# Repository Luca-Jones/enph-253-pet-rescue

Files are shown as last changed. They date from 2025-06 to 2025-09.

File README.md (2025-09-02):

# enph-253-pet-rescue

## Overview
This project is a fully autonomous robot designed for ENPH 253 to compete in the 2025 Engineering Physics Robot Summer Competition at UBC. The cometition theme this year was Pet Rescue and goal was to drive around a course, find animal plushies in need of saving, retrieve them, and return them to the beginning of the course. Our team (team 4) of four Engineering Physics students designed and built the mechanical, electrical, and software components of this robot in 6 weeks to complete these tasks. Our team's strategy was to collect each of the pets into a basket and then lift that basket onto the zip-line to rescue them.

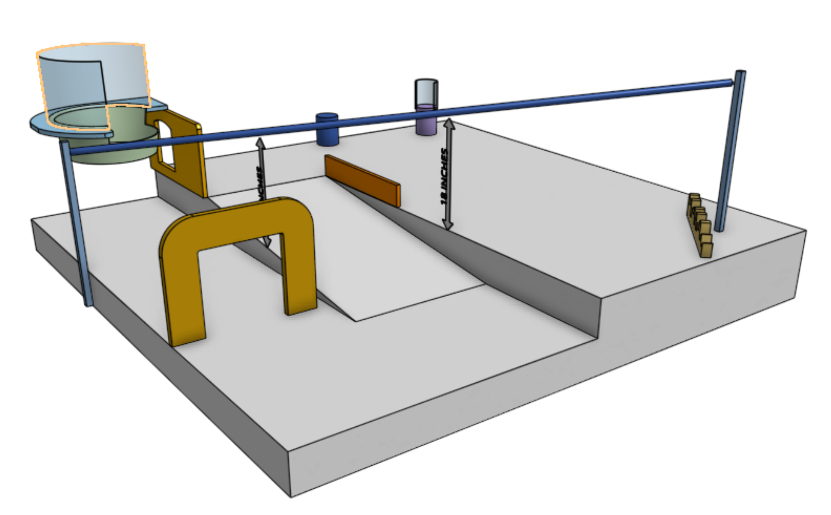
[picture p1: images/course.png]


## Meet the Team

- [Luca Jones](https://github.com/Luca-Jones)
- [Harchetan Chohan](https://github.com/HarchetanChohan)
- [Taichi Kamei](https://github.com/Ta1k25)
- [Coen Molyneaux](https://github.com/Coen-Molyneaux)

## Mechanical Design

The mechanical design was done with Onshape as our CAD tool. It is simple to use and allows for collaboration and version control. Many different manufacturing techniques were used such as 3D printing, laser jet cutting, water jet cutting, lathing, and milling.

### Chassis

The chassis was built out of hardboard and reinforced with water-jet cut aluminium bars. This component required the most communication to perfect as every other part of the robot needs to screw into it.

### Arm

The arm and claw together were responsible for grasping each pet and placing them into the bucket in the rear. The base of the arm is attached to a lazy suzan which is bolted to the chassis, allowing it to easily rotate and pick up pets in different directions. The base also had teeth to mesh with another gear driven by a DC motor. A magnetic rotation encoder was placed underneath the base which provided the feedback needed to create a servo and set an absolute position. The arm is designed as a 4 bar linkage, allowing the servo motors that drive its vertical movement to be located at its base rather than on the hinge. The claw also uses a 4 bar linkage so that the pinsors remain parallel and reach forwards as the claw closes.

### Cascading Lift

The cascading lift mechanism was responsible for lifting the basket that stored each of the pets onto the zip line that would bring them back to the start of the course. The cascading lift works by winding a rope around a spool and extending a cabinet slider through a series of pulleys. This system proved to be extremely effective. Unlike a scissor lift, the mechanical difficulty in lifting happens near the end of the motion rather than at the beginning, allowing us to easily provide enough torque to lift our desired weight.

## Electrical Design

### H-bridge Motor Driver

### IR Sensors

### I2C Buffer and Multiplexer

### Magnetic encoder

## Software Architecture

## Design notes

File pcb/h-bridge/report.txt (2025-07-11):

Error: Update symbol U15 from 'h-bridge-library:Terminal_Block_2POS' to 'h-bridge-library:Terminal_Block_2POS': *** symbol not found ***
Error: Update symbol U16 from 'h-bridge-library:Terminal_Block_2POS' to 'h-bridge-library:Terminal_Block_2POS': *** symbol not found ***
Update symbol R2 from 'Device:R' to 'Device:R': OK
Update symbol #PWR14 from 'power:GND' to 'power:GND': OK
Update symbol R8 from 'Device:R' to 'Device:R': OK
Update symbol #PWR11 from 'power:+3.3V' to 'power:+3.3V': OK
Update symbol U7 from 'h-bridge-library:2N3904' to 'h-bridge-library:2N3904': OK
Update symbol #PWR8 from 'power:GND' to 'power:GND': OK
Update symbol R10 from 'Device:R' to 'Device:R': OK
Update symbol #PWR7 from 'power:GND1' to 'power:GND1': OK
Update symbol R6 from 'Device:R' to 'Device:R': OK
Update symbol #PWR13 from 'power:+3.3V' to 'power:+3.3V': OK
Update symbol U6 from 'h-bridge-library:MCT6' to 'h-bridge-library:MCT6': OK
Update symbol #PWR15 from 'power:+12V' to 'power:+12V': OK
Update symbol U14 from 'h-bridge-library:IRFZ44' to 'h-bridge-library:IRFZ44': OK
Update symbol R13 from 'Device:R' to 'Device:R': OK
Update symbol U12 from 'h-bridge-library:IRFZ44' to 'h-bridge-library:IRFZ44': OK
Update symbol U11 from 'h-bridge-library:IRFZ44' to 'h-bridge-library:IRFZ44': OK
Update symbol U13 from 'h-bridge-library:IRFZ44' to 'h-bridge-library:IRFZ44': OK
Update symbol #PWR21 from 'power:+12V' to 'power:+12V': OK
Update symbol U9 from 'h-bridge-library:IRFZ44' to 'h-bridge-library:IRFZ44': OK
Update symbol C2 from 'Device:C' to 'Device:C': OK
Update symbol C1 from 'Device:C' to 'Device:C': OK
Update symbol U10 from 'h-bridge-library:IRFZ44' to 'h-bridge-library:IRFZ44': OK
Update symbol U8 from 'h-bridge-library:IRFZ44' to 'h-bridge-library:IRFZ44': OK
Update symbol U4 from 'h-bridge-library:IRFZ44' to 'h-bridge-library:IRFZ44': OK
Update symbol #PWR18 from 'power:+12V' to 'power:+12V': OK
Update symbol #PWR16 from 'power:GND' to 'power:GND': OK
Update symbol U17 from 'h-bridge-library:2N3904' to 'h-bridge-library:2N3904': OK
Update symbol R11 from 'Device:R' to 'Device:R': OK
Update symbol #PWR17 from 'power:GND' to 'power:GND': OK
Update symbol #PWR20 from 'power:GND' to 'power:GND': OK
Update symbol U18 from 'h-bridge-library:2N3904' to 'h-bridge-library:2N3904': OK
Update symbol #PWR19 from 'power:+12V' to 'power:+12V': OK
Update symbol R12 from 'Device:R' to 'Device:R': OK
Update symbol #PWR22 from 'power:GND' to 'power:GND': OK
Update symbol R14 from 'Device:R' to 'Device:R': OK
Update symbol U20 from 'h-bridge-library:2N3904' to 'h-bridge-library:2N3904': OK
Update symbol U19 from 'h-bridge-library:2N3904' to 'h-bridge-library:2N3904': OK
Update symbol #PWR23 from 'power:GND' to 'power:GND': OK
Update symbol R4 from 'Device:R' to 'Device:R': OK
Update symbol #PWR4 from 'power:GND' to 'power:GND': OK
Update symbol #PWR33 from 'power:+3.3V' to 'power:+3.3V': OK
Update symbol #PWR35 from 'power:GND1' to 'power:GND1': OK
Update symbol J26 from 'h-bridge-library:B3B-XH-A' to 'h-bridge-library:B3B-XH-A': OK
Update symbol #PWR34 from 'power:GND1' to 'power:GND1': OK
Update symbol J25 from 'h-bridge-library:B3B-XH-A' to 'h-bridge-library:B3B-XH-A': OK
Update symbol R22 from 'Device:R' to 'Device:R': OK
Update symbol R23 from 'Device:R' to 'Device:R': OK
Update symbol R21 from 'Device:R' to 'Device:R': OK
Update symbol R24 from 'Device:R' to 'Device:R': OK
Update symbol U5 from 'h-bridge-library:2N3904' to 'h-bridge-library:2N3904': OK
Update symbol #PWR10 from 'power:+12V' to 'power:+12V': OK
Update symbol #PWR9 from 'power:GND' to 'power:GND': OK
Update symbol #PWR3 from 'power:GND' to 'power:GND': OK
Update symbol R3 from 'Device:R' to 'Device:R': OK
Update symbol #PWR6 from 'power:+3.3V' to 'power:+3.3V': OK
Update symbol #PWR5 from 'power:GND' to 'power:GND': OK
Update symbol R5 from 'Device:R' to 'Device:R': OK
Update symbol #PWR24 from 'power:GND' to 'power:GND': OK
Update symbol R18 from 'Device:R' to 'Device:R': OK
Update symbol R17 from 'Device:R' to 'Device:R': OK
Update symbol U22 from 'h-bridge-library:2N3904' to 'h-bridge-library:2N3904': OK
Update symbol #PWR26 from 'power:GND' to 'power:GND': OK
Update symbol #PWR27 from 'power:+12V' to 'power:+12V': OK
Update symbol #PWR25 from 'power:GND' to 'power:GND': OK
Update symbol U21 from 'h-bridge-library:2N3904' to 'h-bridge-library:2N3904': OK
Update symbol R15 from 'Device:R' to 'Device:R': OK
Update symbol R16 from 'Device:R' to 'Device:R': OK
Update symbol #PWR29 from 'power:+12V' to 'power:+12V': OK
Update symbol R19 from 'Device:R' to 'Device:R': OK
Update symbol #PWR28 from 'power:GND' to 'power:GND': OK
Update symbol U23 from 'h-bridge-library:2N3904' to 'h-bridge-library:2N3904': OK
Update symbol U24 from 'h-bridge-library:2N3904' to 'h-bridge-library:2N3904': OK
Update symbol #PWR30 from 'power:GND' to 'power:GND': OK
Update symbol R20 from 'Device:R' to 'Device:R': OK
Update symbol #PWR31 from 'power:GND' to 'power:GND': OK
Update symbol #PWR32 from 'power:+12V' to 'power:+12V': OK
Update symbol #PWR1 from 'power:GND1' to 'power:GND1': OK
Update symbol U1 from 'h-bridge-library:MCT6' to 'h-bridge-library:MCT6': OK
Update symbol U3 from 'h-bridge-library:LT1161' to 'h-bridge-library:LT1161': OK
Update symbol U2 from 'h-bridge-library:MC33269T-3.3G' to 'h-bridge-library:MC33269T-3.3G': OK
Update symbol #PWR2 from 'power:+3.3V' to 'power:+3.3V': OK
Update symbol R1 from 'Device:R' to 'Device:R': OK
Update symbol R7 from 'Device:R' to 'Device:R': OK
Update symbol R9 from 'Device:R' to 'Device:R': OK
Update symbol #PWR12 from 'power:GND' to 'power:GND': OK

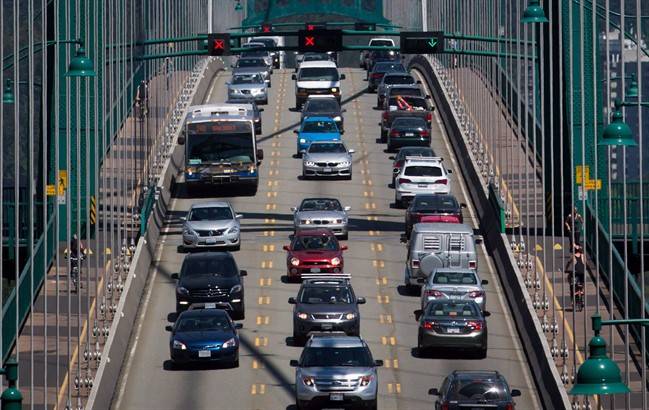
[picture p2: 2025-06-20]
cv-training/traffic.jpg

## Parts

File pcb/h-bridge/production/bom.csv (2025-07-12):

Designator | Footprint | Quantity | Value | LCSC Part #
C1, C2 | C_Disc_D4.3mm_W1.9mm_P5.00mm | 2 | 100nF
C3 | CP_Radial_D5.0mm_P2.50mm | 1 | 0.47uF
C4 | CP_Radial_D5.0mm_P2.50mm | 1 | 10uF
C5, C8, C9 | CP_Radial_D6.3mm_P2.50mm | 3 | 100uF
C6, C7 | C_Disc_D4.3mm_W1.9mm_P5.00mm | 2 | 100pF
J1 | JST_B2B-XH-A | 1 | B2B-XH-A
J2, J3 | JST_S2B-XH-A | 2 | S2B-XH-A
J5 | JST_B5B-XH-A | 1 | B5B-XH-A
R1, R2, R6, R7 | R_Axial_DIN0309_L9.0mm_D3.2mm_P12.70mm_Horizontal | 4 | 330R
R10, R11, R12, R19, R20, R3, R5, R8 | R_Axial_DIN0309_L9.0mm_D3.2mm_P12.70mm_Horizontal | 8 | 10K
R13, R14, R15, R16, R17, R18, R21, R22, R23, R24 | R_Axial_DIN0411_L9.9mm_D3.6mm_P12.70mm_Horizontal | 10 | 100k
R4, R9 | R_Axial_DIN0309_L9.0mm_D3.2mm_P12.70mm_Horizontal | 2 | 1k
U1, U6 | DIP-8_W7.62mm_Socket | 2 | MCT6
U10, U11, U12, U13, U14, U4, U8, U9 | TO-220-3_Vertical | 8 | IRFZ44
U17, U18, U19, U20, U21, U22, U23, U24, U5, U7 | TO-92 | 10 | 2N3904
U2 | TO-220-3_Vertical | 1 | MC33269T-3.3G
U3 | DIP-20_W7.62mm_Socket | 1 | LT1161

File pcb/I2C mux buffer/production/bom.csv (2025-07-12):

Designator | Footprint | Quantity | Value | LCSC Part #
C1, C2, C3 | C_Disc_D3.0mm_W1.6mm_P2.50mm | 3 | 100nF
C4 | C_Disc_D3.0mm_W1.6mm_P2.50mm | 1 | 10uF
J1 | JST_EH_B4B-EH-A_1x04_P2.50mm_Vertical | 1 | ToF Chassis
J2 | JST_EH_B4B-EH-A_1x04_P2.50mm_Vertical | 1 | ToF Claw
J3 | JST_PH_B5B-PH-K_1x05_P2.00mm_Vertical | 1 | Raspberry Pi
R1, R2, R3, R4, R5 | R_Axial_DIN0309_L9.0mm_D3.2mm_P12.70mm_Horizontal | 5 | 1k
R6 | R_Axial_DIN0309_L9.0mm_D3.2mm_P12.70mm_Horizontal | 1 | 10k
U1 | TSSOP-24_4.4x7.8mm_P0.65mm | 1 | TCA9548APWR
U2 | DGK0008A | 1 | TCA9617ADGKR

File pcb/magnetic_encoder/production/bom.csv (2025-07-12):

Designator | Footprint | Quantity | Value | LCSC Part #
C1 | C_Disc_D3.0mm_W1.6mm_P2.50mm | 1 | 100nF
C2 | CP_Radial_D5.0mm_P2.50mm | 1 | 10uF
J1 | JST_EH_S2B-EH_1x02_P2.50mm_Horizontal | 1 | Conn_01x02_Pin
J2 | JST_EH_S4B-EH_1x04_P2.50mm_Horizontal | 1 | Conn_01x04_Pin
R1, R2 | R_Axial_DIN0207_L6.3mm_D2.5mm_P7.62mm_Horizontal | 2 | 4.7K
U1 | SOIC-8_3.9x4.9mm_P1.27mm | 1 | ~

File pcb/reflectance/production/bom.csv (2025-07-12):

Designator | Footprint | Quantity | Value | LCSC Part #
J1, J2, J3 | JST_EH_B4B-EH-A_1x04_P2.50mm_Vertical | 3 | JCT 4pin
J4, J7 | JST_EH_B4B-EH-A_1x04_P2.50mm_Vertical | 2 | Reflectance Sensor 4
J6 | JST_EH_B3B-EH-A_1x03_P2.50mm_Vertical | 1 | Conn_01x03_Pin
J8 | JST_EH_B5B-EH-A_1x05_P2.50mm_Vertical | 1 | Conn_01x05_Pin
R1, R10, R15, R4, R7 | R_Axial_DIN0207_L6.3mm_D2.5mm_P7.62mm_Horizontal | 5 | 47k
R11, R14, R2, R5, R8 | R_Axial_DIN0207_L6.3mm_D2.5mm_P7.62mm_Horizontal | 5 | 330R
R12, R16, R3, R6, R9 | R_Axial_DIN0207_L6.3mm_D2.5mm_P7.62mm_Horizontal | 5 | 1k
RV1 | Potentiometer_Bourns_3296W_Vertical | 1 | 100k
U1, U2, U3, U4, U5 | DIP-8_W7.62mm_Socket_LongPads | 5 | LM311

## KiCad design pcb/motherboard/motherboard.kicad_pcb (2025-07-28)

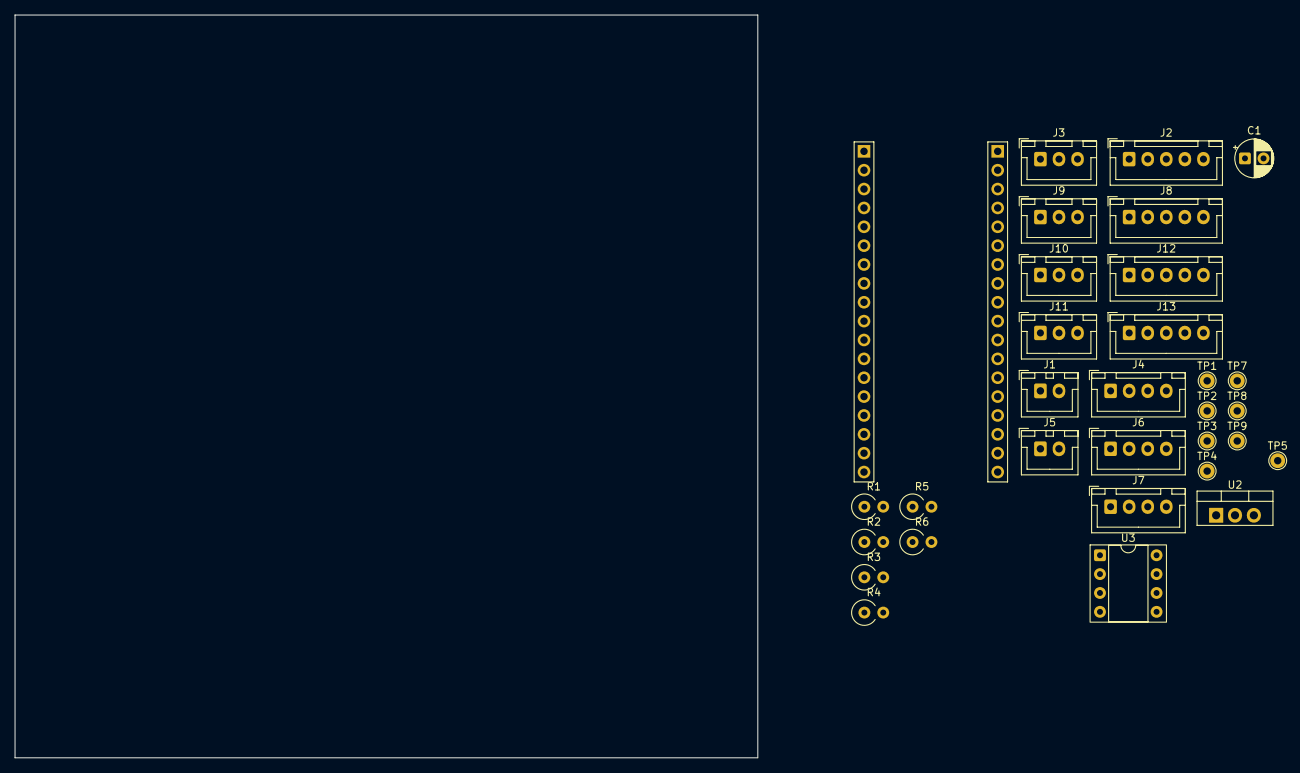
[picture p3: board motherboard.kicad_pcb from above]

Board: 2 copper layers, 100.0 x 100.0 mm, 31 parts (0 on the bottom side), 36 nets, no tracks yet.

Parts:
C1: 0.47uF; CP_Radial_D5.0mm_P2.50mm
J1, J5: B2B-XH-A; JST_XH_B2B-XH-A_1x02_P2.50mm_Vertical
J2, J8, J12, J13: B5B-XH-A; JST_XH_B5B-XH-A_1x05_P2.50mm_Vertical
J3, J9, J10, J11: B3B-XH-A; JST_XH_B3B-XH-A_1x03_P2.50mm_Vertical
J4, J6, J7: B4B-XH-A; JST_XH_B4B-XH-A_1x04_P2.50mm_Vertical
R1, R6: 1k; R_Axial_DIN0309_L9.0mm_D3.2mm_P2.54mm_Vertical
R2, R3, R4, R5: 100k; R_Axial_DIN0309_L9.0mm_D3.2mm_P2.54mm_Vertical
TP1: GPIO1; TestPoint_THTPad_D2.0mm_Drill1.0mm
TP2: GPIO3; TestPoint_THTPad_D2.0mm_Drill1.0mm
TP3: GPIO7; TestPoint_THTPad_D2.0mm_Drill1.0mm
TP4: GPIO8; TestPoint_THTPad_D2.0mm_Drill1.0mm
TP5: GPIO20; TestPoint_THTPad_D2.0mm_Drill1.0mm
TP7: GPIO 0; TestPoint_THTPad_D2.0mm_Drill1.0mm
TP8: GPIO 39; TestPoint_THTPad_D2.0mm_Drill1.0mm
TP9: GPIO 36; TestPoint_THTPad_D2.0mm_Drill1.0mm
U1: ESP32 PICO KIT; ESP32_PICO_KIT
U2: UA9805; TO-220-3_Vertical
U3: LM311; DIP-8_W7.62mm_Socket

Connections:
+3V3: J3.3, J4.1, J6.1, J7.1, J8.1, R1.1, R6.1, U1.1 (3V3), U1.21 (3V3)
+5V: J3.1, R3.2, U1.19 (5V), U2.3 (VOUT), U3.8 (V+)
+8V: J1.1, J9.1, J10.1, J11.1, U2.1 (VIN)
/BASE GEAR MOTOR DIR: J13.2, U1.31 (32)
/BASE GEAR MOTOR PWM: J13.1, U1.30 (33)
/BIG ARM SERVO: J9.2, U1.23 (4)
/CASCADE MOTOR DIR: J13.5, U1.33 (25)
/CASCADE MOTOR PWM: J13.4, U1.32 (26)
/CLAW SERVO: J11.2, U1.25 (15(BOOT_PULLUP))
/ECHO: J4.2, U1.11 (10)
/IR1: J2.1, U1.4 (37)
/IR2: J2.2, U1.5 (38)
/IR3: J2.3, U1.6 (34)
/IR4: J2.4, U1.7 (35)
/IR5: J2.5, U1.10 (9)
/LEFT MOTOR DIR: J12.2, U1.27 (12(BOOT_PULLDOWN))
/LEFT MOTOR PWM: J12.1, U1.26 (13)
/RIGHT MOTOR DIR: J12.5, U1.29 (27)
/RIGHT MOTOR PWM: J12.4, U1.28 (14)
/SCL: J6.2, J7.2, J8.2, U1.16 (22)
/SDA: J6.3, J7.3, J8.3, U1.17 (21)
/SMALL ARM SERVO: J10.2, U1.24 (2(BOOT_PULLDOWN))
/SWITCH1: R5.1, R6.2, U1.15 (19), U3.7
/TRIG: J4.3, U1.12 (5(BOOT_PULLUP))
GND: C1.2, J1.2, J3.2, J4.4, J5.2, J6.4, J7.4, J8.4, J8.5, J9.3, J10.3, J11.3, J12.3, J13.3, R4.1, U1.2 (GND), U1.20 (GND), U1.36 (GND), U2.2 (GND), U3.1 (GND), U3.4 (V-)
unnamed: J5.1, R1.2, R2.1
unnamed: TP7.1, U1.22 (0(BOOT_PULLUP))
unnamed: TP3.1, U1.13 (7)
unnamed: TP4.1, U1.14 (8)
unnamed: TP5.1, U1.18 (20)
unnamed: TP2.1, U1.9 (RX0(GPIO3))
unnamed: TP1.1, U1.8 (TX0(GPIO1))
unnamed: TP8.1, U1.34 (VN(GPIO39))
unnamed: TP9.1, U1.35 (VP(GPIO36))
unnamed: R3.1, R4.2, R5.2, U3.2 (+)
unnamed: C1.1, R2.2, U3.3 (-)

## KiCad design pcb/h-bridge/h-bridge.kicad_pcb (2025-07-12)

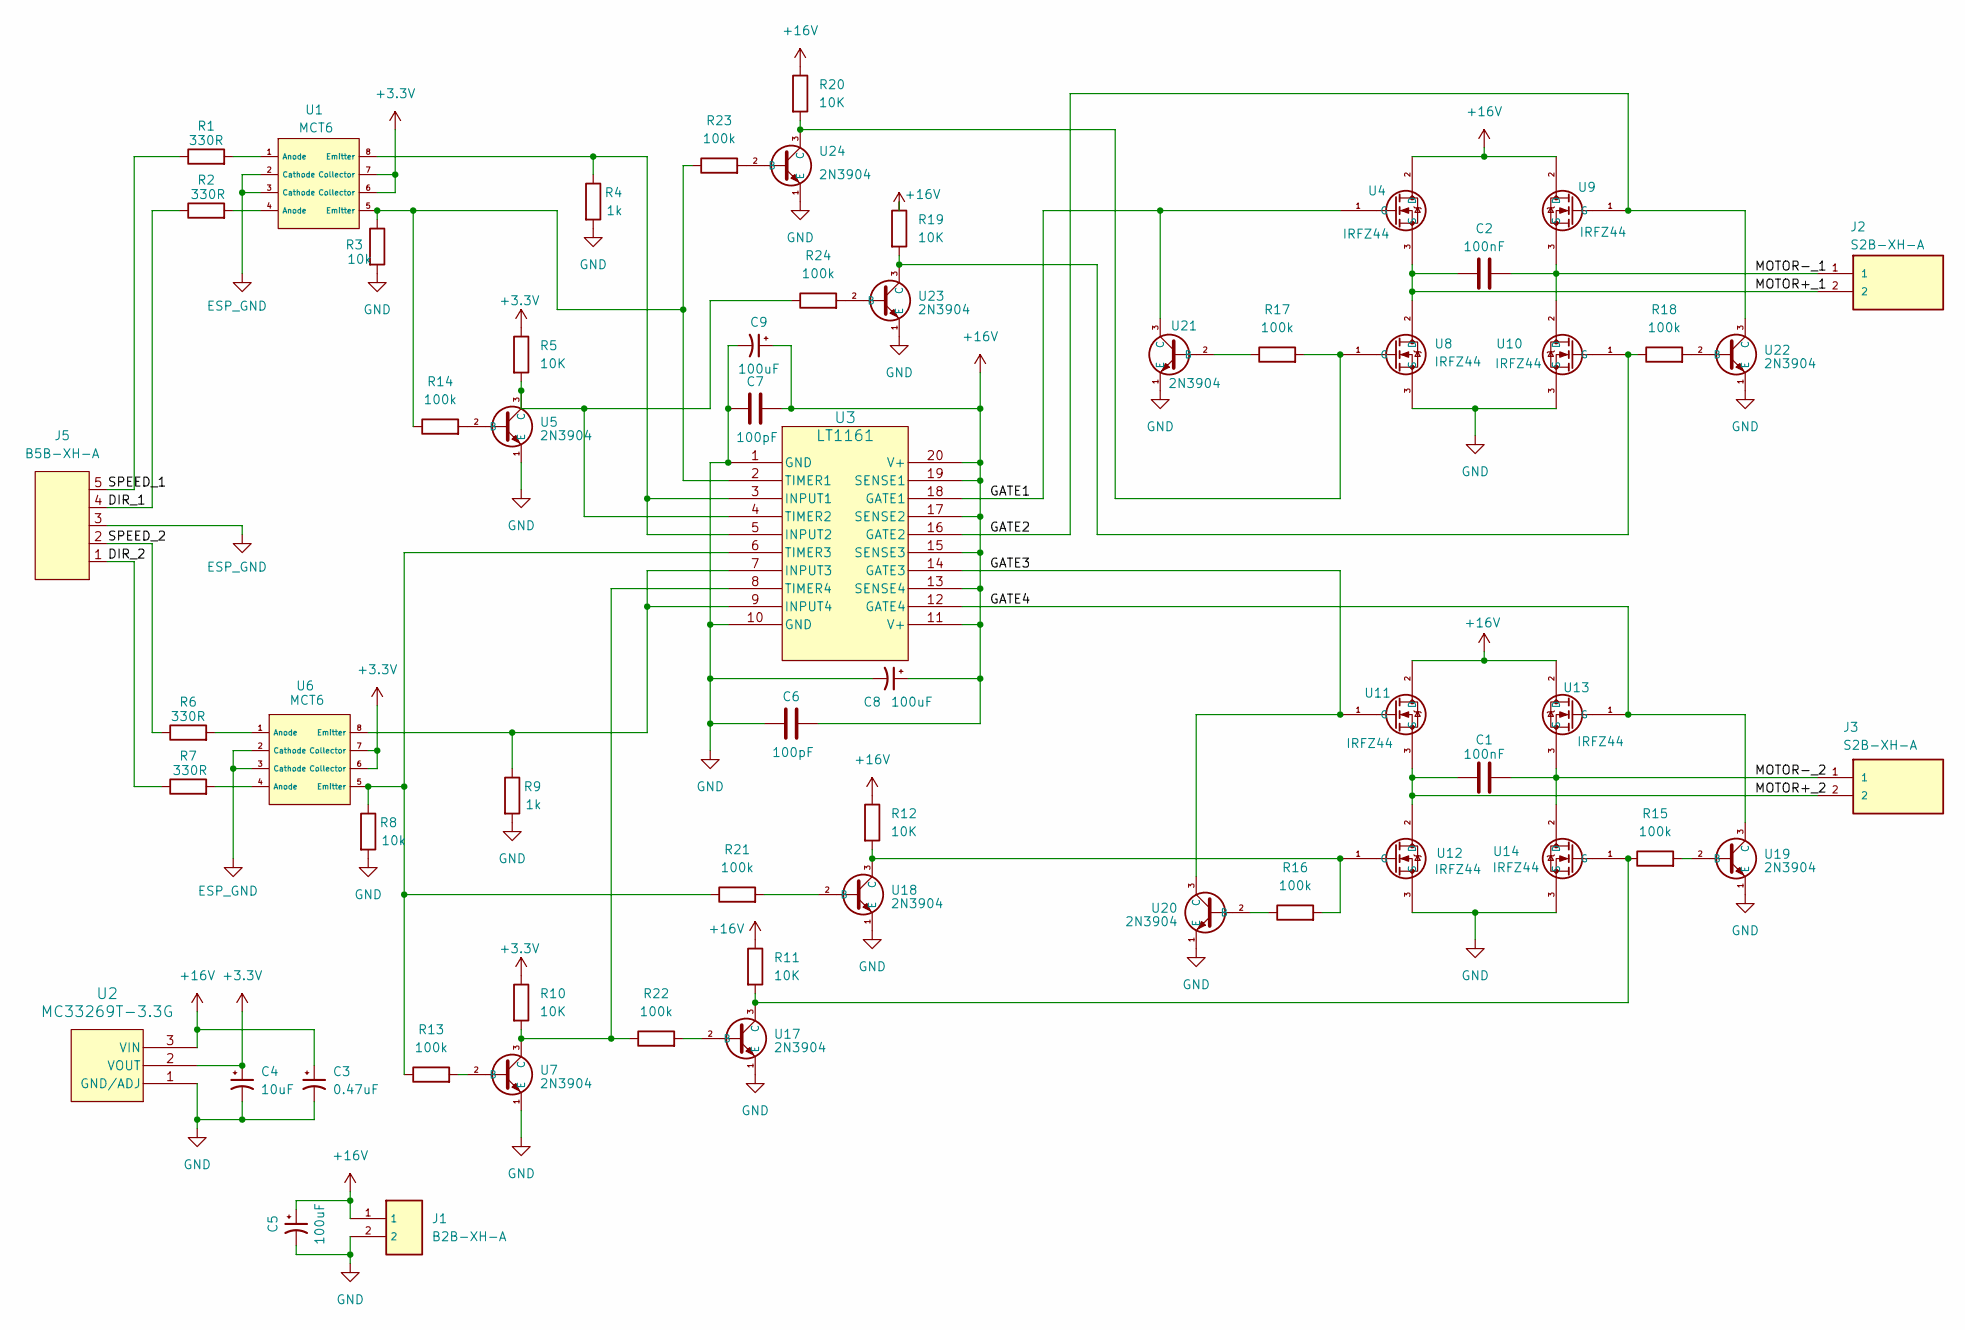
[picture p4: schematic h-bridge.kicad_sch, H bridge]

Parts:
C1, C2: 100nF; C_Disc_D3.0mm_W1.6mm_P2.50mm
C3: 0.47uF; CP_Radial_D5.0mm_P2.50mm
C4: 10uF; CP_Radial_D5.0mm_P2.50mm
C5, C8, C9: 100uF; CP_Radial_D6.3mm_P2.50mm
C6, C7: 100pF; C_Disc_D3.0mm_W1.6mm_P2.50mm
J1: B2B-XH-A; JST_B2B-XH-A
J2, J3: S2B-XH-A; JST_S2B-XH-A
J5: B5B-XH-A; JST_B5B-XH-A
R1, R2, R6, R7: 330R; R_Axial_DIN0309_L9.0mm_D3.2mm_P12.70mm_Horizontal
R3, R8: 10k; R_Axial_DIN0309_L9.0mm_D3.2mm_P12.70mm_Horizontal
R4, R9: 1k; R_Axial_DIN0309_L9.0mm_D3.2mm_P12.70mm_Horizontal
R5, R10, R11, R12, R19, R20: 10K; R_Axial_DIN0309_L9.0mm_D3.2mm_P12.70mm_Horizontal
R13, R14, R15, R16, R17, R18, R21, R22, R23, R24: 100k; R_Axial_DIN0411_L9.9mm_D3.6mm_P12.70mm_Horizontal
U1, U6: MCT6; DIP-8_W7.62mm_Socket
U2: MC33269T-3.3G; TO-220-3_Vertical
U3: LT1161; DIP-20_W7.62mm_Socket
U4, U8, U9, U10, U11, U12, U13, U14: IRFZ44; TO-220-3_Vertical
U5, U7, U17, U18, U19, U20, U21, U22, U23, U24: 2N3904; TO-92

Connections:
+3.3V: C4.1, R5.1, R10.1, U1.6 (Collector), U1.7 (Collector), U2.2 (VOUT), U6.6 (Collector), U6.7 (Collector)
+16V: C3.1, C5.1, C6.2, C7.2, C8.1, C9.1, J1.1, R11.1, R12.1, R19.1, R20.1, U2.3 (VIN), U3.11 (V+), U3.13 (SENSE4), U3.15 (SENSE3), U3.17 (SENSE2), U3.19 (SENSE1), U3.20 (V+), U4.2 (D), U9.2 (D), U11.2 (D), U13.2 (D)
/DIR_1: J5.4, R2.1
/DIR_2: J5.1, R7.1
/GATE1: U3.18 (GATE1), U4.1 (G), U21.3 (C)
/GATE2: U3.16 (GATE2), U9.1 (G), U22.3 (C)
/GATE3: U3.14 (GATE3), U11.1 (G), U20.3 (C)
/GATE4: U3.12 (GATE4), U13.1 (G), U19.3 (C)
/MOTOR+_1: C2.1, J2.2, U4.3 (S), U8.2 (D)
/MOTOR+_2: C1.1, J3.2, U11.3 (S), U12.2 (D)
/MOTOR-_1: C2.2, J2.1, U9.3 (S), U10.2 (D)
/MOTOR-_2: C1.2, J3.1, U13.3 (S), U14.2 (D)
/SPEED_1: J5.5, R1.1
/SPEED_2: J5.2, R6.1
ESP_GND: J5.3, U1.2 (Cathode), U1.3 (Cathode), U6.2 (Cathode), U6.3 (Cathode)
GND: C3.2, C4.2, C5.2, C6.1, C7.1, C8.2, C9.2, J1.2, R3.2, R4.2, R8.2, R9.2, U2.1 (GND/ADJ), U3.1 (GND), U3.10 (GND), U5.1 (E), U7.1 (E), U8.3 (S), U10.3 (S), U12.3 (S), U14.3 (S), U17.1 (E), U18.1 (E), U19.1 (E), U20.1 (E), U21.1 (E), U22.1 (E), U23.1 (E), U24.1 (E)
unnamed: R1.2, U1.1 (Anode)
unnamed: R2.2, U1.4 (Anode)
unnamed: R6.2, U6.1 (Anode)
unnamed: R7.2, U6.4 (Anode)
unnamed: R4.1, U1.8 (Emitter), U3.3 (INPUT1), U3.5 (INPUT2)
unnamed: R9.1, U3.7 (INPUT3), U3.9 (INPUT4), U6.8 (Emitter)
unnamed: R3.1, R14.1, R23.1, U1.5 (Emitter), U3.2 (TIMER1)
unnamed: R5.2, R24.1, U3.4 (TIMER2), U5.3 (C)
unnamed: R8.1, R13.1, R21.1, U3.6 (TIMER3), U6.5 (Emitter)
unnamed: R10.2, R22.1, U3.8 (TIMER4), U7.3 (C)
unnamed: R14.2, U5.2 (B)
unnamed: R13.2, U7.2 (B)
unnamed: R18.1, R19.2, U10.1 (G), U23.3 (C)
unnamed: R12.2, R16.2, U12.1 (G), U18.3 (C)
unnamed: R11.2, R15.1, U14.1 (G), U17.3 (C)
unnamed: R22.2, U17.2 (B)
unnamed: R21.2, U18.2 (B)
unnamed: R15.2, U19.2 (B)
unnamed: R16.1, U20.2 (B)
unnamed: R17.1, U21.2 (B)
unnamed: R18.2, U22.2 (B)
unnamed: R24.2, U23.2 (B)
unnamed: R23.2, U24.2 (B)
unnamed: R17.2, R20.2, U8.1 (G), U24.3 (C)

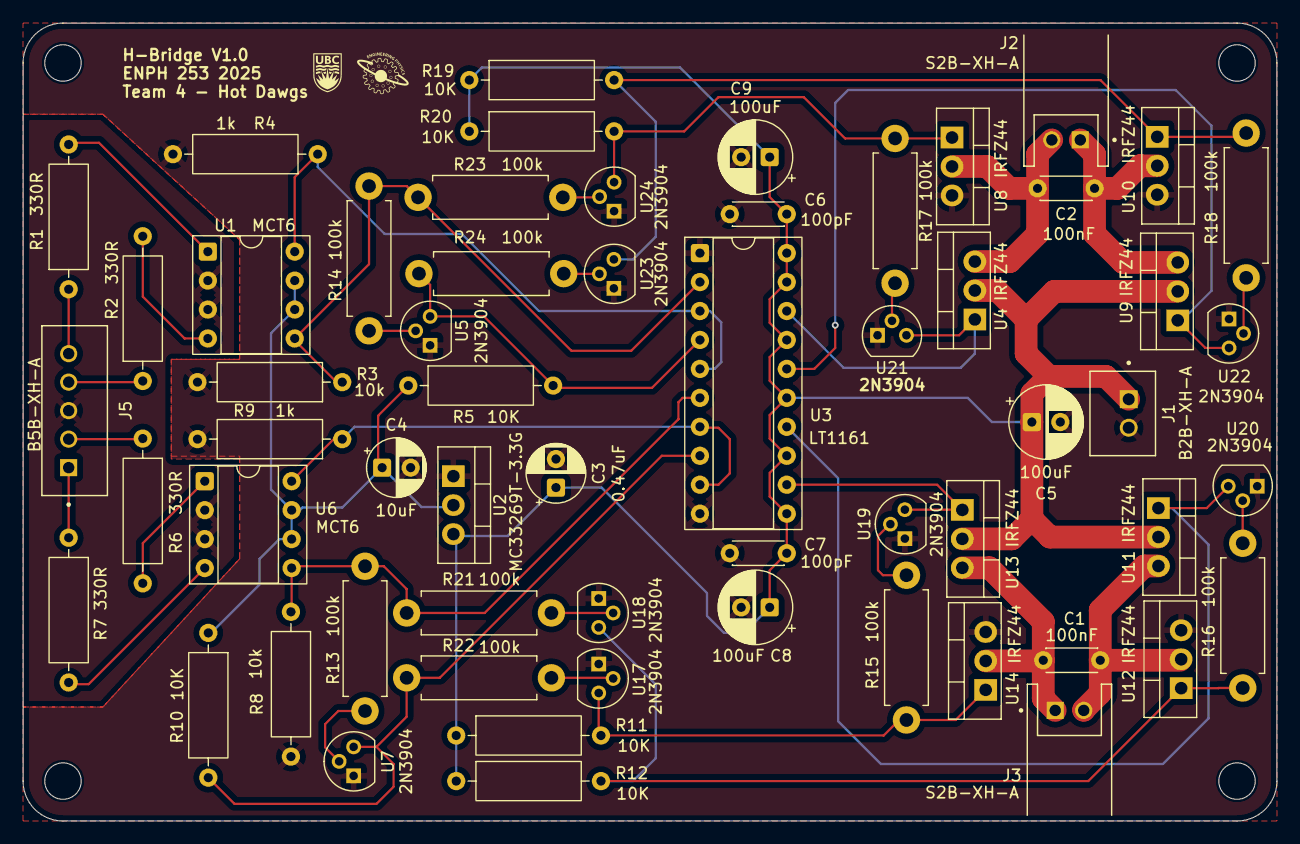
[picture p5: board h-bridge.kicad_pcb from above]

Board: 2 copper layers, 110.0 x 70.0 mm, 59 parts (0 on the bottom side), 40 nets.

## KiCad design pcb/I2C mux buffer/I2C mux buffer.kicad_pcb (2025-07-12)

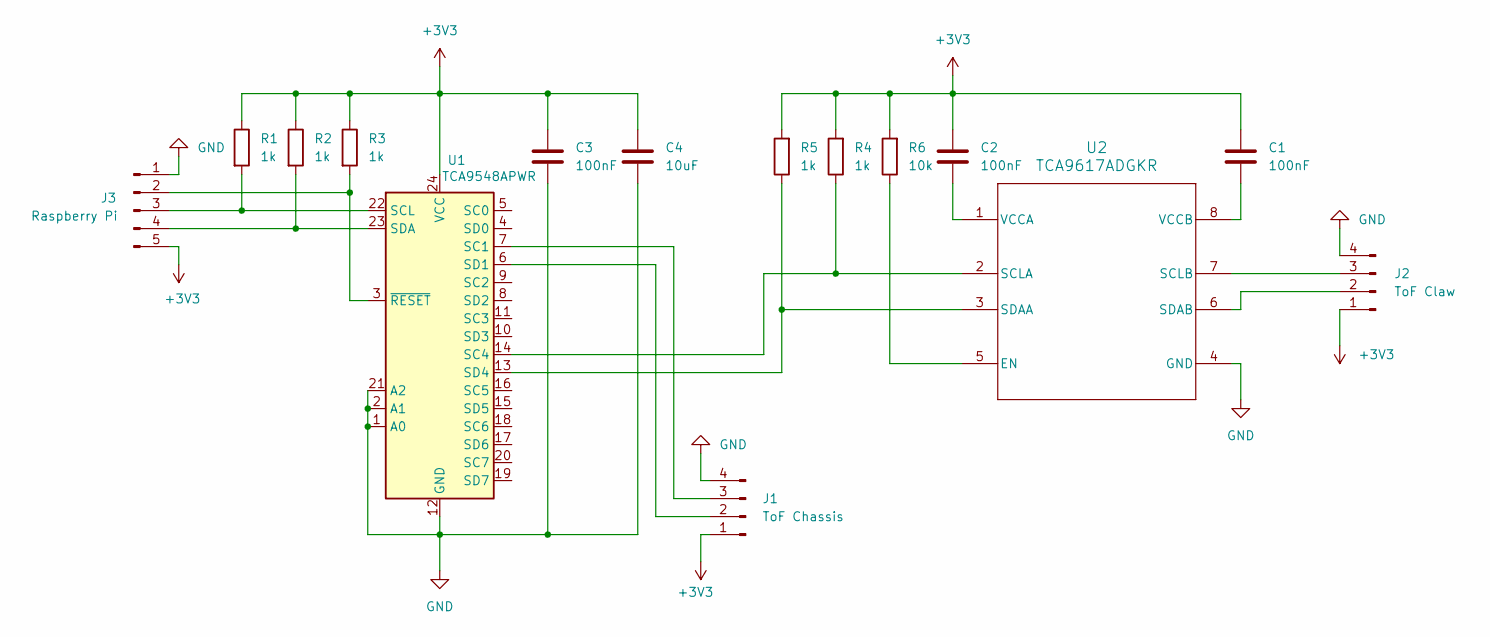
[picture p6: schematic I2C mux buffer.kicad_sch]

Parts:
C1, C2, C3: 100nF; C_Disc_D3.0mm_W1.6mm_P2.50mm
C4: 10uF; C_Disc_D3.0mm_W1.6mm_P2.50mm
J1: ToF Chassis; JST_EH_B4B-EH-A_1x04_P2.50mm_Vertical
J2: ToF Claw; JST_EH_B4B-EH-A_1x04_P2.50mm_Vertical
J3: Raspberry Pi; JST_PH_B5B-PH-K_1x05_P2.00mm_Vertical
R1, R2, R3, R4, R5: 1k; R_Axial_DIN0309_L9.0mm_D3.2mm_P12.70mm_Horizontal
R6: 10k; R_Axial_DIN0309_L9.0mm_D3.2mm_P12.70mm_Horizontal
U1: TCA9548APWR; TSSOP-24_4.4x7.8mm_P0.65mm
U2: TCA9617ADGKR; DGK0008A

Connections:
+3V3: C1.1, C2.1, C3.1, C4.1, J1.1, J2.1, J3.5, R1.1, R2.1, R3.1, R4.2, R5.2, R6.2, U1.24 (VCC)
GND: C3.2, C4.2, J1.4, J2.4, J3.1, U1.1 (A0), U1.2 (A1), U1.12 (GND), U1.21 (A2), U2.4 (GND)
unnamed: J1.2, U1.6 (SD1)
unnamed: J1.3, U1.7 (SC1)
unnamed: J2.2, U2.6 (SDAB)
unnamed: J2.3, U2.7 (SCLB)
unnamed: J3.2, R3.2, U1.3 (~RESET)
unnamed: J3.3, R1.2, U1.22 (SCL)
unnamed: J3.4, R2.2, U1.23 (SDA)
unnamed: R4.1, U1.14 (SC4), U2.2 (SCLA)
unnamed: R5.1, U1.13 (SD4), U2.3 (SDAA)
unnamed: R6.1, U2.5 (EN)
unnamed: C2.2, U2.1 (VCCA)
unnamed: C1.2, U2.8 (VCCB)

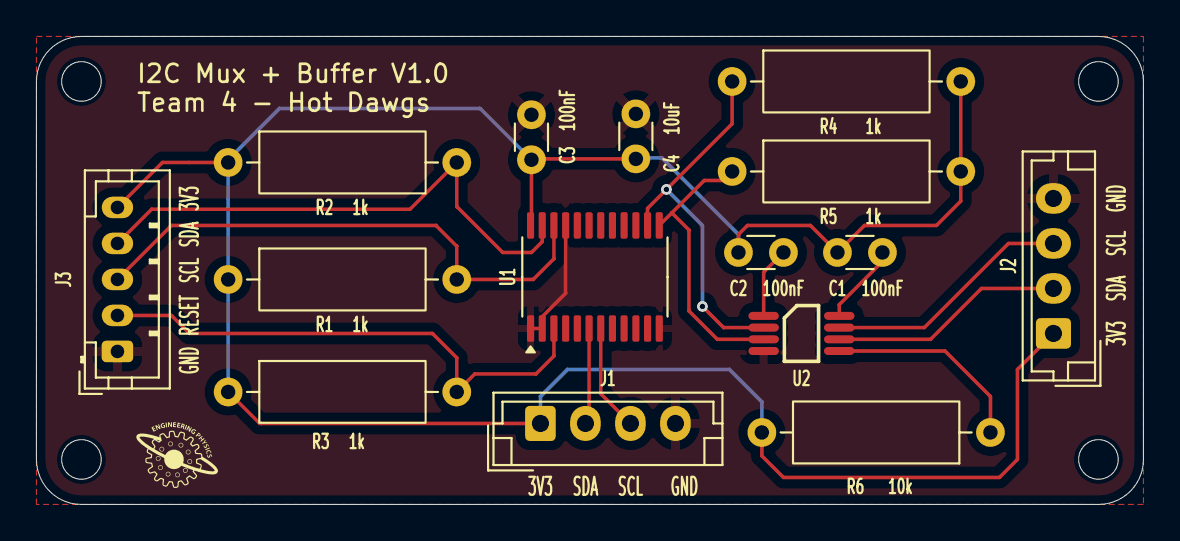
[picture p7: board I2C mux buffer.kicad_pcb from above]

Board: 2 copper layers, 61.5 x 26.0 mm, 15 parts (0 on the bottom side), 14 nets.

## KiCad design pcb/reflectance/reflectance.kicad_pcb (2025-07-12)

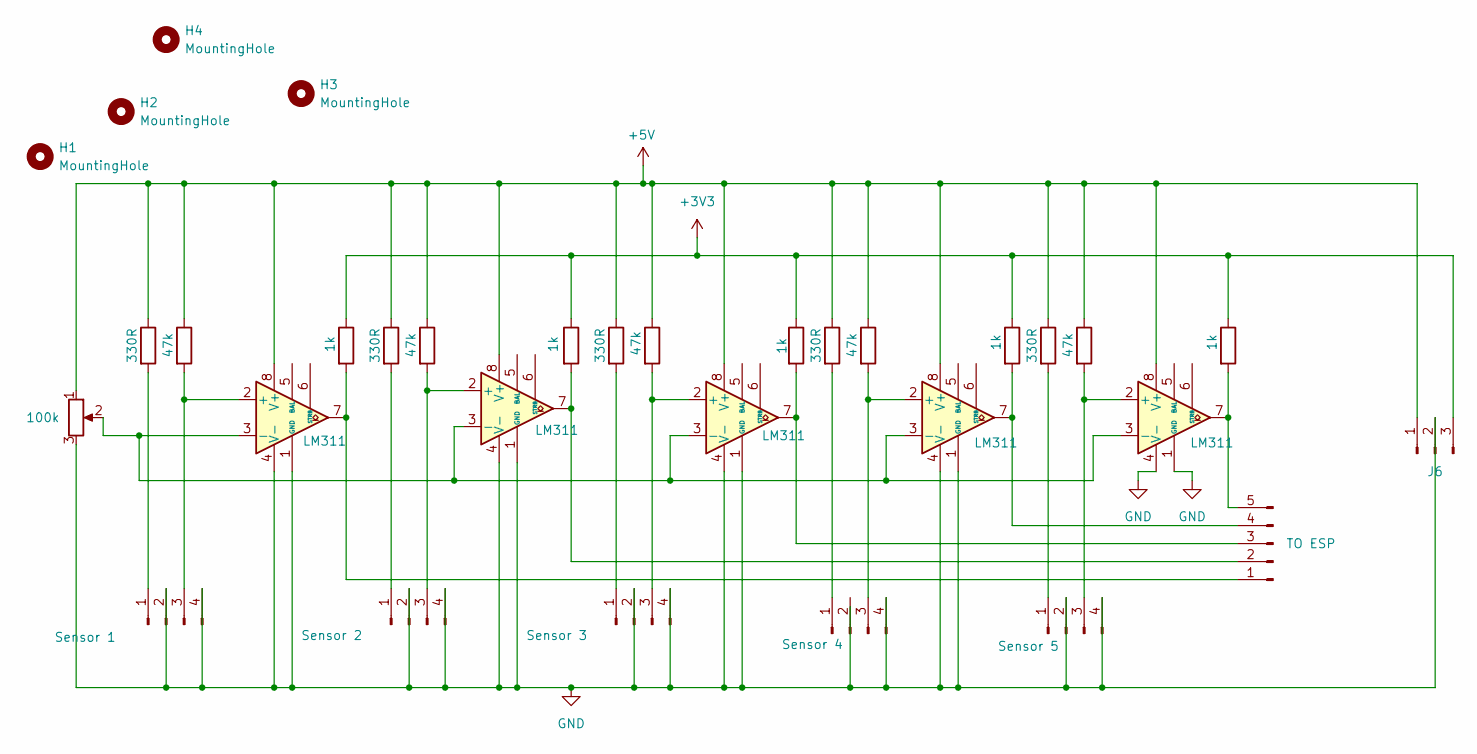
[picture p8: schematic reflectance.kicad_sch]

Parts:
H1, H2, H3, H4: MountingHole; MountingHole_3.2mm_M3
J1, J3: JCT 4pin; JST_EH_B4B-EH-A_1x04_P2.50mm_Vertical
J2: JCt 4pin; JST_EH_B4B-EH-A_1x04_P2.50mm_Vertical
J4, J7: Reflectance Sensor 4; JST_EH_B4B-EH-A_1x04_P2.50mm_Vertical
J6: Conn_01x03_Pin; JST_EH_B3B-EH-A_1x03_P2.50mm_Vertical
J8: Conn_01x05_Pin; JST_EH_B5B-EH-A_1x05_P2.50mm_Vertical
R1, R4, R7, R10, R15: 47k; R_Axial_DIN0207_L6.3mm_D2.5mm_P7.62mm_Horizontal
R2, R5, R8, R11, R14: 330R; R_Axial_DIN0207_L6.3mm_D2.5mm_P7.62mm_Horizontal
R3, R6, R9, R12, R16: 1k; R_Axial_DIN0207_L6.3mm_D2.5mm_P7.62mm_Horizontal
RV1: 100k; Potentiometer_Bourns_3296W_Vertical
U1, U2, U3, U4, U5: LM311; DIP-8_W7.62mm_Socket_LongPads

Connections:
+3V3: J6.3, R3.1, R6.1, R9.1, R12.1, R16.1
+5V: J6.1, R1.1, R2.1, R4.1, R5.1, R7.1, R8.1, R10.1, R11.1, R14.1, R15.1, RV1.1, U1.8 (V+), U2.8 (V+), U3.8 (V+), U4.8 (V+), U5.8 (V+)
GND: J1.2, J1.4, J2.2, J2.4, J3.2, J3.4, J4.4, J6.2, J7.2, J7.4, RV1.3, U1.1 (GND), U1.4 (V-), U2.1 (GND), U2.4 (V-), U3.1 (GND), U3.4 (V-), U4.1 (GND), U4.4 (V-), U5.1 (GND), U5.4 (V-)
unnamed: J1.1, R2.2
unnamed: J1.3, R1.2, U2.2 (+)
unnamed: J2.1, R5.2
unnamed: J2.3, R4.2, U1.2 (+)
unnamed: J3.1, R8.2
unnamed: J3.3, R7.2, U3.2 (+)
unnamed: J4.1, R11.2
unnamed: J4.3, R10.2, U4.2 (+)
unnamed: J7.1, R14.2
unnamed: J7.3, R15.2, U5.2 (+)
unnamed: J8.1, R3.2, U2.7
unnamed: J8.2, R6.2, U1.7
unnamed: J8.3, R9.2, U3.7
unnamed: J8.4, R12.2, U4.7
unnamed: J8.5, R16.2, U5.7
unnamed: RV1.2, U1.3 (-), U2.3 (-), U3.3 (-), U4.3 (-), U5.3 (-)

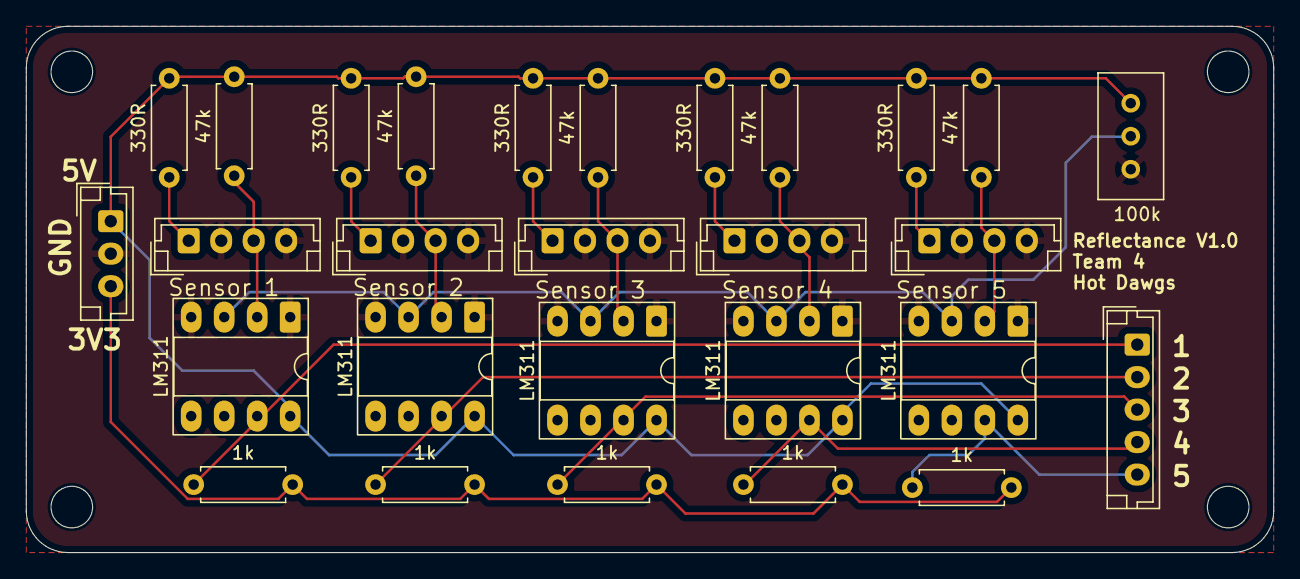
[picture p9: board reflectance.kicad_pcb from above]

Board: 2 copper layers, 96.0 x 40.5 mm, 32 parts (0 on the bottom side), 19 nets.

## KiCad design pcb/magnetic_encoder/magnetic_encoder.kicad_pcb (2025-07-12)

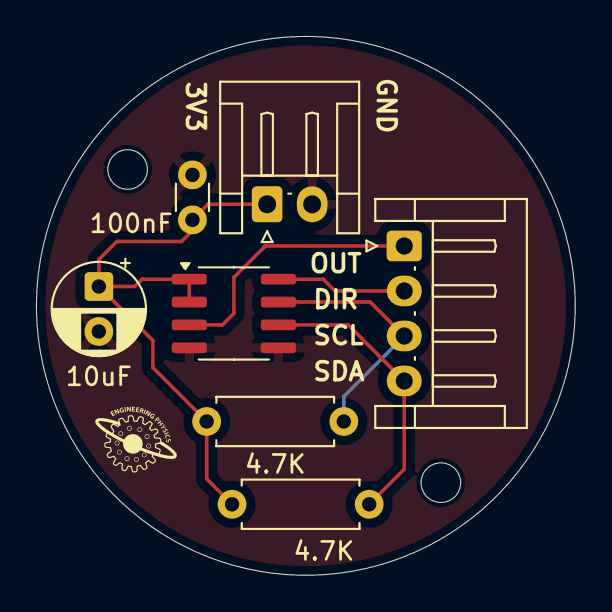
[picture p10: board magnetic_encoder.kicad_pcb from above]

Board: 2 copper layers, 29.9 x 29.9 mm, 9 parts (0 on the bottom side), 6 nets.

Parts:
C1: 100nF; C_Disc_D3.0mm_W1.6mm_P2.50mm
C2: 10uF; CP_Radial_D5.0mm_P2.50mm
H1, H3: MountingHole; MountingHole_2.2mm_M2
J1: Conn_01x02_Pin; JST_EH_S2B-EH_1x02_P2.50mm_Horizontal
J2: Conn_01x04_Pin; JST_EH_S4B-EH_1x04_P2.50mm_Horizontal
R1, R2: 4.7K; R_Axial_DIN0207_L6.3mm_D2.5mm_P7.62mm_Horizontal
U1: SOIC-8_3.9x4.9mm_P1.27mm

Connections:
+3.3V: C1.1, C2.1, J1.1, R1.1, R2.1, U1.1 (VDD5V), U1.2 (VDD3V3)
GND: C1.2, C2.2, J1.2, U1.4 (GND), U1.5 (PGO)
unnamed: J2.1, U1.3 (OUT)
unnamed: J2.2, U1.8 (DIR)
unnamed: J2.3, R2.2, U1.7 (SCL)
unnamed: J2.4, R1.2, U1.6 (SDA)

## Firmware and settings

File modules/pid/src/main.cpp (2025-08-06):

#include <WebServer.h>
#include <WiFi.h>
#include <Arduino.h>


// WiFi credentials
const char *ssid = "hot_dawgs_esp";
const char *password = "team4_da_best_on_top";


#define FORWARD LOW
#define BACKWARD HIGH


// Web server
WebServer server(80);


// PID parameters (tunable via web or serial)
float Kp = 25.0, Ki = 0.0, Kd = 0.0;
float recoveryRatio = 0.6; // Ratio of base speed for recovery spin
float targetPosition = 0.0;
float currentPosition = 0.0;
float previousError = 0.0;
float integral = 0.0;
float lastPosition = 0.0;
float deadband = 0.1;
float integralDecay = 0.95;
float maxIntegral = 100.0;
bool targetChanged = false;


unsigned long lastPIDTime = 0;
bool lastPID[5];
unsigned long sampleTime = 30;


const int SENSOR_LEFT_LEFT = 37;
const int SENSOR_LEFT      = 38;
const int SENSOR_CENTER    = 34;
const int SENSOR_RIGHT     = 35;
const int SENSOR_RIGHT_RIGHT = 9;


const int MOTOR_LEFT_PWM  = 14;
const int MOTOR_LEFT_DIR  = 27;
const int MOTOR_RIGHT_PWM = 13;
const int MOTOR_RIGHT_DIR = 12;


const int PWM_FREQ = 1000;
const int PWM_RESOLUTION = 8;
const int PWM_CHANNEL_LEFT = 0;
const int PWM_CHANNEL_RIGHT = 1;


int baseSpeed = 100;
int maxSpeed = 255;
int minSpeed = 0;


// Tasks
TaskHandle_t wifiTaskHandle;
TaskHandle_t controlTaskHandle;


// HTML page
const char htmlPage[] PROGMEM = R"rawliteral(
<!DOCTYPE html>
<html>
<head>
   <title>ESP32 PID Tuning</title>
   <style>
     body { font-family: sans-serif; margin: 20px; }
     .controls { margin-bottom: 20px; }
     .control-group { margin: 10px 0; }
     label { margin-right: 10px; }
     input[type="number"] { width: 80px; padding: 5px; }
     button { padding: 8px 16px; background: #007bff; color: white; border: none; cursor: pointer; }
     button:hover { background: #0056b3; }
     .sensor-values {
       margin: 20px 0;
       padding: 10px;
       background: #f8f9fa;
       border-radius: 5px;
     }
     .sensor {
       display: inline-block;
       margin: 0 10px;
       text-align: center;
     }
     .sensor-indicator {
       width: 20px;
       height: 20px;
       border-radius: 50%;
       margin: 5px auto;
       background-color: #ddd;
     }
     .sensor-active {
       background-color: #28a745;
     }
     .status {
       margin: 20px 0;
       padding: 10px;
       background: #e9ecef;
       border-radius: 5px;
     }
   </style>
</head>
<body>
   <h2>ESP32 PID Tuning</h2>


   <div class="sensor-values">
     <h3>Sensor Values</h3>
     <div class="sensor">
       <div id="sensor-ll" class="sensor-indicator"></div>
       <div>LL</div>
     </div>
     <div class="sensor">
       <div id="sensor-l" class="sensor-indicator"></div>
       <div>L</div>
     </div>
     <div class="sensor">
       <div id="sensor-c" class="sensor-indicator"></div>
       <div>C</div>
     </div>
     <div class="sensor">
       <div id="sensor-r" class="sensor-indicator"></div>
       <div>R</div>
     </div>
     <div class="sensor">
       <div id="sensor-rr" class="sensor-indicator"></div>
       <div>RR</div>
     </div>
   </div>


   <div class="status">
     <h3>Status</h3>
     <p>Current Position: <span id="current-pos">0.0</span></p>
     <p>Error: <span id="error">0.0</span></p>
     <p>PID Output: <span id="pid-output">0.0</span></p>
   </div>


   <div class="controls">
     <div class="control-group">
       <label>Kp: <input id="kp" type="number" value="100.0" step="0.1"></label>
       <label>Ki: <input id="ki" type="number" value="0.5" step="0.1"></label>
       <label>Kd: <input id="kd" type="number" value="20.0" step="0.1"></label>
       <button onclick="setPID()">Set PID</button>
     </div>
    
     <div class="control-group">
       <label>Recovery Ratio: <input id="recovery-ratio" type="number" value="0.6" step="0.1" min="0.1" max="1.0"></label>
       <button onclick="setRecoveryRatio()">Set Recovery Ratio</button>
     </div>
    
     <div class="control-group">
       <label>Base Speed: <input id="base-speed" type="number" value="100" min="0" max="255"></label>
       <button onclick="setSpeed()">Set Speed</button>
     </div>
   </div>
    <script>
     function setPID() {
       const kp = document.getElementById('kp').value;
       const ki = document.getElementById('ki').value;
       const kd = document.getElementById('kd').value;
       fetch(`/setPID?kp=${kp}&ki=${ki}&kd=${kd}`)
         .then(response => {
           if (!response.ok) {
             console.error('Failed to set PID parameters');
           }
         })
         .catch(error => console.error('Error:', error));
     }
      function setRecoveryRatio() {
       const ratio = document.getElementById('recovery-ratio').value;
       fetch(`/setRecoveryRatio?value=${ratio}`)
         .then(response => {
           if (!response.ok) {
             console.error('Failed to set recovery ratio');
           }
         })
         .catch(error => console.error('Error:', error));
     }
    
     function setSpeed() {
       const speed = document.getElementById('base-speed').value;
       fetch(`/setSpeed?value=${speed}`)
         .then(response => {
           if (!response.ok) {
             console.error('Failed to set speed');
           }
         })
         .catch(error => console.error('Error:', error));
     }
      function updateSensors(sensors) {
       document.getElementById('sensor-ll').className = 'sensor-indicator' + (sensors.ll ? ' sensor-active' : '');
       document.getElementById('sensor-l').className = 'sensor-indicator' + (sensors.l ? ' sensor-active' : '');
       document.getElementById('sensor-c').className = 'sensor-indicator' + (sensors.c ? ' sensor-active' : '');
       document.getElementById('sensor-r').className = 'sensor-indicator' + (sensors.r ? ' sensor-active' : '');
       document.getElementById('sensor-rr').className = 'sensor-indicator' + (sensors.rr ? ' sensor-active' : '');
     }
    
     function updateStatus(data) {
       document.getElementById('current-pos').textContent = data.current.toFixed(2);
       document.getElementById('error').textContent = data.error.toFixed(2);
       document.getElementById('pid-output').textContent = data.output.toFixed(2);
     }


     function update() {
       fetch('/status')
         .then(res => res.json())
         .then(data => {
           updateSensors(data.sensors);
           updateStatus(data);
         })
         .catch(error => {
           console.error('Error fetching status:', error);
         });
     }
      window.addEventListener('load', function() {
       setInterval(update, 200);
     });
   </script>
</body>
</html>
)rawliteral";


// ==== Helper Functions ====


void controlMotors(float pidOutput) {
 int leftSpeed = baseSpeed - pidOutput;
 int rightSpeed = baseSpeed + pidOutput;


 leftSpeed = constrain(leftSpeed, -maxSpeed, maxSpeed);
 rightSpeed = constrain(rightSpeed, -maxSpeed, maxSpeed);


 // Stop motors first
 ledcWrite(PWM_CHANNEL_LEFT, 0);
 ledcWrite(PWM_CHANNEL_RIGHT, 0);
 delayMicroseconds(100);


 // Set directions
 digitalWrite(MOTOR_LEFT_DIR, leftSpeed >= 0 ? FORWARD : BACKWARD);
 digitalWrite(MOTOR_RIGHT_DIR, rightSpeed >= 0 ? FORWARD : BACKWARD);
 delayMicroseconds(100);


 // Apply PWM values
 ledcWrite(PWM_CHANNEL_LEFT, abs(leftSpeed));
 ledcWrite(PWM_CHANNEL_RIGHT, abs(rightSpeed));
}


float calculateError(bool ll, bool l, bool c, bool r, bool rr) {
 float totalWeight = 0;
 float weightedSum = 0;


 if (ll) { totalWeight += 1.0; weightedSum += -2; }
 if (l)  { totalWeight += 1.0; weightedSum += -1; }
 if (c)  { totalWeight += 1.0; weightedSum += 0; }
 if (r)  { totalWeight += 1.0; weightedSum += 1; }
 if (rr) { totalWeight += 1.0; weightedSum += 2; }


 if (totalWeight == 0) return currentPosition; // No line detected, maintain last position
 return weightedSum / totalWeight;
}


void recoverySpin() {
 // Spin right to find line
 digitalWrite(MOTOR_LEFT_DIR, FORWARD);
 digitalWrite(MOTOR_RIGHT_DIR, BACKWARD);
 ledcWrite(PWM_CHANNEL_LEFT, baseSpeed * recoveryRatio);
 ledcWrite(PWM_CHANNEL_RIGHT, baseSpeed * recoveryRatio);
}


void offTapeCorrection(bool lastLeft){
 if (lastLeft) {
   digitalWrite(MOTOR_LEFT_DIR, BACKWARD);
   digitalWrite(MOTOR_RIGHT_DIR, FORWARD);
   ledcWrite(PWM_CHANNEL_LEFT, baseSpeed * recoveryRatio);
   ledcWrite(PWM_CHANNEL_RIGHT, baseSpeed * recoveryRatio);
 } else {
   digitalWrite(MOTOR_LEFT_DIR, FORWARD);
   digitalWrite(MOTOR_RIGHT_DIR, BACKWARD);
   ledcWrite(PWM_CHANNEL_LEFT, baseSpeed * recoveryRatio);
   ledcWrite(PWM_CHANNEL_RIGHT, baseSpeed * recoveryRatio);
 }
}


// ==== Tasks ====


void wifiTask(void *pvParameters) {
 server.on("/", []() {
   server.send_P(200, "text/html", htmlPage);
 });


 server.on("/setPID", []() {
   if (server.hasArg("kp")) Kp = server.arg("kp").toFloat();
   if (server.hasArg("ki")) Ki = server.arg("ki").toFloat();
   if (server.hasArg("kd")) Kd = server.arg("kd").toFloat();
   integral = 0; // Reset integral when PID changes
   server.send(200, "text/plain", "OK");
 });


 server.on("/setRecoveryRatio", []() {
   if (server.hasArg("value")) {
     recoveryRatio = server.arg("value").toFloat();
     recoveryRatio = constrain(recoveryRatio, 0.1, 1.0);
   }
   server.send(200, "text/plain", "OK");
 });
  server.on("/setSpeed", []() {
   if (server.hasArg("value")) {
     baseSpeed = server.arg("value").toInt();
     baseSpeed = constrain(baseSpeed, 0, 255);
   }
   server.send(200, "text/plain", "OK");
 });


 server.on("/status", []() {
   float error = targetPosition - currentPosition;
   float pTerm = Kp * error;
   float iTerm = Ki * integral;
   float dTerm = Kd * (lastPosition - currentPosition);
   float output = pTerm + iTerm + dTerm;
  
   String json = "{\"current\":" + String(currentPosition, 2) +
                 ",\"error\":" + String(error, 2) +
                 ",\"output\":" + String(output, 2) +
                 ",\"sensors\":{" +
                 "\"ll\":" + (digitalRead(SENSOR_LEFT_LEFT) ? "true" : "false") +
                 ",\"l\":" + (digitalRead(SENSOR_LEFT) ? "true" : "false") +
                 ",\"c\":" + (digitalRead(SENSOR_CENTER) ? "true" : "false") +
                 ",\"r\":" + (digitalRead(SENSOR_RIGHT) ? "true" : "false") +
                 ",\"rr\":" + (digitalRead(SENSOR_RIGHT_RIGHT) ? "true" : "false") +
                 "}}";
   server.send(200, "application/json", json);
 });


 server.begin();


 while (true) {
   server.handleClient();
   vTaskDelay(pdMS_TO_TICKS(10));
 }
}


void controlTask(void *pvParameters) {
 // Setup pins
 pinMode(SENSOR_LEFT_LEFT, INPUT);
 pinMode(SENSOR_LEFT, INPUT);
 pinMode(SENSOR_CENTER, INPUT);
 pinMode(SENSOR_RIGHT, INPUT);
 pinMode(SENSOR_RIGHT_RIGHT, INPUT);
  pinMode(MOTOR_LEFT_DIR, OUTPUT);
 pinMode(MOTOR_RIGHT_DIR, OUTPUT);
  // Setup PWM
 ledcSetup(PWM_CHANNEL_LEFT, PWM_FREQ, PWM_RESOLUTION);
 ledcSetup(PWM_CHANNEL_RIGHT, PWM_FREQ, PWM_RESOLUTION);
 ledcAttachPin(MOTOR_LEFT_PWM, PWM_CHANNEL_LEFT);
 ledcAttachPin(MOTOR_RIGHT_PWM, PWM_CHANNEL_RIGHT);


 unsigned long lastPrint = 0;
 lastPIDTime = millis();


 while (true) {
   unsigned long now = millis();
  
   // PID control runs at specified sample time
   if (now - lastPIDTime >= sampleTime) {
     // Read sensors
     bool sLL = digitalRead(SENSOR_LEFT_LEFT);
     bool sL  = digitalRead(SENSOR_LEFT);
     bool sC  = digitalRead(SENSOR_CENTER);
     bool sR  = digitalRead(SENSOR_RIGHT);
     bool sRR = digitalRead(SENSOR_RIGHT_RIGHT);


     float output, error, pTerm, iTerm, dTerm;
     if (!sLL && !sL && !sC && !sR && !sRR) {
         float lastLL = lastPID[0];
         float lastRR = lastPID[4];


         if (lastLL){
           controlMotors(baseSpeed * recoveryRatio);
         }
         if (lastRR){
           controlMotors(baseSpeed * recoveryRatio * -1);
         }
     } else{
       currentPosition = calculateError(sLL, sL, sC, sR, sRR);
    
       // Calculate error
       float error = targetPosition - currentPosition;
        // PID calculations
       float deltaTime = (now - lastPIDTime) / 1000.0; // Convert to seconds
      
       // Proportional term
       float pTerm = Kp * error;
      
       // Integral term with decay and limits
       integral = integral * integralDecay + (error * deltaTime);
       integral = constrain(integral, -maxIntegral, maxIntegral);
       float iTerm = Ki * integral;
      
       // Derivative term (on measurement to avoid derivative kick)
       float dTerm = Kd * (lastPosition - currentPosition) / deltaTime;
       lastPosition = currentPosition;
      
       // Calculate final output
       output = pTerm + iTerm + dTerm;


       controlMotors(output);


       if (now - lastPrint > 500) {
         Serial.printf("LL:%d L:%d C:%d R:%d RR:%d | Pos:%.2f | Err:%.2f | P:%.2f I:%.2f D:%.2f | Out:%.2f\n",
                       sLL, sL, sC, sR, sRR,
                       currentPosition, error, pTerm, iTerm, dTerm, output);
         lastPrint = now;
       }
     }
    
     lastPIDTime = now;


     lastPID[0] = sLL;
     lastPID[1] = sL;
     lastPID[2] = sC;
     lastPID[3] = sR;
     lastPID[4] = sRR;


   }


   vTaskDelay(pdMS_TO_TICKS(1));
 }
}


// ==== Main Setup ====


void setup() {
 Serial.begin(115200);
  // Set up WiFi Access Point
 WiFi.softAP(ssid, password);
 IPAddress apIP = WiFi.softAPIP();


 Serial.println("Access Point Started");
 Serial.print("Connect to WiFi: ");
 Serial.println(ssid);
 Serial.print("Then open browser to: http://");
 Serial.println(apIP);


 // Create tasks on different cores
 xTaskCreatePinnedToCore(wifiTask, "WiFiTask", 8192, NULL, 1, &wifiTaskHandle, 0);
 xTaskCreatePinnedToCore(controlTask, "ControlTask", 4096, NULL, 2, &controlTaskHandle, 1);
}


void loop() {
 // Nothing needed in loop - tasks handle everything
 delay(1000);
}

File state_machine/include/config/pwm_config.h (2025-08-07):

#ifndef PWM_CONFIG_H
#define PWM_CONFIG_H

#define PWM_CHANNEL_SERVO_1         14          // timer 3      50 Hz
#define PWM_CHANNEL_SERVO_2         15          // timer 3      50 Hz
#define PWM_CHANNEL_SERVO_3         6           // timer 3      50 Hz
#define PWM_CHANNEL_MOTOR_LEFT      12          // timer 2      1 kHz
#define PWM_CHANNEL_MOTOR_RIGHT     13          // timer 2      1 kHz
#define PWM_CHANNEL_CASCADE         8           // timer 0      1 kHz
#define PWM_CHANNEL_BASE_GEAR       11          // timer 1      50 Hz

#define PWM_FRQ_HZ_MOTOR_LEFT       1000
#define PWM_FRQ_HZ_MOTOR_RIGHT      1000
#define PWM_FRQ_HZ_CASCADE          1000
#define PWM_FRQ_HZ_BASE_GEAR        50

#define PWM_RESOLUTION_MOTOR_LEFT   8
#define PWM_RESOLUTION_MOTOR_RIGHT  8
#define PWM_RESOLUTION_CASCADE      8
#define PWM_RESOLUTION_BASE_GEAR    8

#define PWM_MAX_DUTY_MOTOR_LEFT     1 << PWM_RESOLUTION_MOTOR_LEFT
#define PWM_MAX_DUTY_MOTOR_RIGHT    1 << PWM_RESOLUTION_MOTOR_RIGHT
#define PWM_MAX_DUTY_CASCADE        1 << PWM_RESOLUTION_CASCADE
#define PWM_MIN_DUTY_BASE_GEAR      60
#define PWM_MAX_DUTY_BASE_GEAR      65
#endif

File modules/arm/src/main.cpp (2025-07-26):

#include <Arduino.h>
#include <Arm.h>
#include <Servo.h>

#define POT_PIN_1 33
#define POT_PIN_2 26
#define BUTTON_PIN 27

#define CLAW_PIN 4
#define CLAW_ANGLE_MAX 180

Servo servo_1(ARM_SERVO_1_ANGLE_MAX);
Servo servo_2(ARM_SERVO_2_ANGLE_MAX);
Servo claw(CLAW_ANGLE_MAX);
volatile bool is_claw_closed = false;
Arm arm(&servo_1, &servo_2);
volatile bool button_pressed = false;
volatile int counter = 0;


// IRAM safe code
void IRAM_ATTR switchPressedISR() {
    button_pressed = gpio_get_level((gpio_num_t) BUTTON_PIN);
    if(!button_pressed) {
        counter++;
        is_claw_closed = !is_claw_closed;
    }
}

void setup() {
    pinMode(BUTTON_PIN, INPUT_PULLUP);
    attachInterrupt(digitalPinToInterrupt(BUTTON_PIN), switchPressedISR, CHANGE);
    Serial.begin(115200);
    Serial.setTimeout(1000000);
    servo_1.attach(ARM_SERVO_1_PIN, ARM_SERVO_1_CHANNEL, 500, 2500);
    servo_2.attach(ARM_SERVO_2_PIN, ARM_SERVO_2_CHANNEL, 500, 2500);
    claw.attach(CLAW_PIN, 3, 500, 2500);

}

void log_pos() {
    int theta_1; int theta_2; float phi_1; float phi_2; int x; int y;
    arm.log_pos(&theta_1, &theta_2, &phi_1, &phi_2, &x, &y);
    Serial.printf("x = %d, y = %d\nphi_1 = %f, phi_2 = %f\ntheta_1 = %d, theta_2 = %d\n\n\n", x, y, phi_1, phi_2, theta_1, theta_2);
}

void calibrate() {
    String input = Serial.readStringUntil('\n');
    Serial.println(input);
    servo_1.write(input.toInt());
}

void loop() {

    calibrate();
    
    // claw.write(140);
    // arm.lerp_to_pos(250,50,250);
    // log_pos();
    // delay(1000);
    // arm.lerp_to_pos(250,200,250);
    // delay(500);
    // arm.lerp_to_pos(350,200,250);
    // delay(500);
    // claw.write(95);
    // delay(500);
    // arm.lerp_to_pos(220,210,250);
    // delay(500);
    // arm.lerp_to_pos(220,300,250);
    // delay(500);
    // claw.write(180);
    // delay(5000);

    // claw.write(180);
    // arm.lerp_to_pos(250,50,250);
    // delay(1500);
    // arm.lerp_to_pos(250,100,250);
    // delay(500);
    // arm.lerp_to_pos(350,100,250);
    // delay(500);
    // claw.write(100);
    // delay(500);
    // arm.lerp_to_pos(350,300,250);
    // delay(500);
    // arm.lerp_to_pos(180,300,250);
    // delay(500);
    // claw.write(180);
    // delay(5000);
    
}

// if (button_pressed) {
//     Serial.println(counter);
//     if (is_claw_closed) {
//         claw.write(110);
//         Serial.println("Claw CLOSED");
//     } else {
//         claw.write(180);
//         Serial.println("Claw OPEN");
//     }
// }
// button_pressed = false;

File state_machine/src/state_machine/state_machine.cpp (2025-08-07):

#include <Arduino.h>
#include <driver/timer.h>

#include <state_machine/state_machine.h>
#include <state_machine/state_close_claw.h>
#include <state_machine/state_reach.h>
#include <state_machine/state_retreat.h>
#include <state_machine/state_return_pets.h>
#include <state_machine/state_store.h>
#include <state_machine/state_tape_following.h>
#include <state_machine/state_wait.h>
#include <state_machine/state_drop_off.h>

#include <config/dir_config.h>

#define ARRAY_SIZE(array) (sizeof(array) / sizeof(array[0]))

/*
    Author: Luca Jones
    Date:   July 2025

    This is a state machine implemented with enums and functions.
    The robot moves between states through Transitions, which are triggered by Events.
    The event that ocurred is determined by the sensors.

    1. Process the sensor input and return the appropriate event
    2. Process the event and change the state accordingly
    3. Run a step of that state's routine
    4. Repeat

*/

/* Actuators */
Servo servo_1(ARM_SERVO_1_ANGLE_MAX);
Servo servo_2(ARM_SERVO_2_ANGLE_MAX);
Arm arm(&servo_1, &servo_2);
Servo claw(180);
Motor base_gear_motor(PIN_BASE_GEAR_PWM, PWM_CHANNEL_BASE_GEAR, PWM_FRQ_HZ_BASE_GEAR, PWM_RESOLUTION_BASE_GEAR, PIN_BASE_GEAR_DIR);
BaseGear base_gear = BaseGear(&base_gear_motor);
Motor left_motor(PIN_MOTOR_LEFT_PWM, PWM_CHANNEL_MOTOR_LEFT, PWM_FRQ_HZ_MOTOR_LEFT, PWM_RESOLUTION_MOTOR_LEFT, PIN_MOTOR_LEFT_DIR);
Motor right_motor(PIN_MOTOR_RIGHT_PWM, PWM_CHANNEL_MOTOR_RIGHT, PWM_FRQ_HZ_MOTOR_RIGHT, PWM_RESOLUTION_MOTOR_RIGHT, PIN_MOTOR_RIGHT_DIR);
Motor cascade_motor(PIN_CASCADE_PWM, PWM_CHANNEL_CASCADE, PWM_FRQ_HZ_CASCADE, PWM_RESOLUTION_CASCADE, PIN_CASCADE_DIR);
#define TAPE_FOLLOWING_DEFAULT_SPEED 60

/* Sensors */
SemaphoreHandle_t i2c_mutex;
volatile state_event_e tof_reading;
// SemaphoreHandle_t tof_reading_mutex;
TaskHandle_t tof_task_handle = NULL;
TaskHandle_t dist_task_handle = NULL;
ToF tof_claw;
ToF tof_chassis;
ToF_data tof_data_claw;
ToF_data tof_data_chassis;
volatile bool switch_triggered = false;
volatile bool ramp_detected = false;
volatile int tape_following_base_speed;
volatile int last_tape_following_base_speed;

/* STATE TRANSITIONS */
struct state_transition {
    state_e previous_state;
    state_event_e event;
    state_e next_state;
};

// consult the diagram to understand these transitions
static const struct state_transition state_transitions[] = {
    
    {   STATE_TAPE_FOLLOWING,   EVENT_PET_DETECTED_LEFT,    STATE_REACH             },
    {   STATE_TAPE_FOLLOWING,   EVENT_PILLAR_DETECTED,      STATE_REACH             },
    {   STATE_TAPE_FOLLOWING,   EVENT_PET_DETECTED_RIGHT,   STATE_REACH             },
    {   STATE_REACH,            EVENT_PET_NEAR,             STATE_CLOSE_CLAW        },
    {   STATE_CLOSE_CLAW,       EVENT_PET_GRASPED,          STATE_STORE             },
    {   STATE_CLOSE_CLAW,       EVENT_FIRST_PET_GRASPED,    STATE_TAPE_FOLLOWING    },
    {   STATE_TAPE_FOLLOWING,   EVENT_RAMP,                 STATE_DROP_OFF          },
    {   STATE_DROP_OFF,         EVENT_PET_STORED,           STATE_TAPE_FOLLOWING    },
    {   STATE_STORE,            EVENT_PET_STORED,           STATE_TAPE_FOLLOWING    },
    {   STATE_TAPE_FOLLOWING,   EVENT_EDGE_DETECTED,        STATE_RETURN_PETS       },
    {   STATE_RETURN_PETS,      EVENT_PETS_RETURNED,        STATE_WAIT              },
};


/* FUNCTIONS */
static void state_enter (struct state_machine *state_machine, state_e next_state, state_event_e event);
static void state_exit  (struct state_machine *state_machine, state_e previous_state);

bool IRAM_ATTR timer_isr_callback (void *args) {
    ramp_detected = true;
    return true;
}

void state_machine_init(struct state_machine *state_machine) {
    
    // set up state machine data
    state_machine->state = STATE_TAPE_FOLLOWING;
    state_machine->internal_event = EVENT_NONE;

    state_machine->stable_pet_count_left    = 0;
    state_machine->stable_pet_count_right   = 0;
    state_machine->stable_pillar_count      = 0;

    state_machine->pets_stored              = 0;
    state_machine->arm_in_start_pos         = true;
    state_machine->claw_closed              = false;
    state_machine->claw_open_angle          = CLAW_OPEN;
    state_machine->attempts                 = 0;

    state_machine->last_error               = 0;
    state_machine->last_pid_time            = 0;
    state_machine->last_ir_ll               = false;
    state_machine->last_ir_l                = false;
    state_machine->last_ir_c                = false;
    state_machine->last_ir_r                = false;
    state_machine->last_ir_rr               = false;
    state_machine->no_ir_counter            = 0;

    timer_config_t timer_config = {
        .alarm_en = TIMER_ALARM_EN,
        .counter_en = TIMER_PAUSE,
        .counter_dir = TIMER_COUNT_UP,
        .auto_reload = TIMER_AUTORELOAD_DIS,
        .divider = 16,
    };
    timer_init(TIMER_GROUP_0, TIMER_0, &timer_config);
    timer_set_counter_value(TIMER_GROUP_0, TIMER_0, 0);
    timer_set_alarm_value(TIMER_GROUP_0, TIMER_0, RAMP_TIME_S * TIMER_BASE_CLK / 16);
    timer_enable_intr(TIMER_GROUP_0, TIMER_0);
    timer_isr_callback_add(TIMER_GROUP_0, TIMER_0, timer_isr_callback, 0, 0);

    // set up I2C
    Wire.begin(PIN_I2C_SDA, PIN_I2C_SCL);
    Wire.setClock(I2C_FRQ_HZ);

    i2c_mutex = xSemaphoreCreateMutex();
    if (i2c_mutex == NULL) {
        #ifdef DEBUG
        Serial.println("Failed to create I2C mutex!");
        #endif
        return; // Exit initialization if mutex creation fails
    } else {
        #ifdef DEBUG
        Serial.println("I2C mutex created sucessfully!");
        #endif
    }
    
    tof_reading = EVENT_NONE;
    
    // set up ToF FIRST (before creating tasks that use them)
    #ifdef DEBUG
    Serial.println("Setting up ToF claw sensor...");
    #endif
    tof_setup(&tof_claw, TOF_CHANNEL_CLAW);
    
    #ifdef DEBUG
    Serial.println("Setting up ToF chassis sensor...");
    #endif
    tof_setup(&tof_chassis, TOF_CHANNEL_CHASSIS);

    BaseType_t dist_task_result = xTaskCreatePinnedToCore(
        dist_input_task,
        "dist Task",
        12288,                 // Increased stack size from 8192 to 12288 (12KB)
        NULL,
        1,
        &dist_task_handle,
        0
    );
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

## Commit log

2025-06-28 improved groundpet detection
2025-07-05 Servo library v1 written for the claw
2025-07-11 added pcb dir
    [h-bridge-B_Cu.gbr, h-bridge-B_Mask.gbr, h-bridge-B_Paste.gbr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]
2025-07-11 I2C Mux Bufffer
    [I2C mux buffer.kicad_pcb, I2C mux buffer.kicad_sch]
2025-07-12 pcbs reviewed
    [I2C mux buffer-B_Cu.gbr, I2C mux buffer-B_Mask.gbr, I2C mux buffer-B_Paste.gbr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]
2025-07-12 expanded h-bridge ground plane
    [h-bridge.kicad_pcb]
2025-07-13 attempted calibration of the arm
2025-07-15 arm moves nicely now
2025-07-15 added uart messaging into ToF python code
2025-07-15 arm ready to move after tof is tested
2025-07-15 Updated pid code with wifi tuning
2025-07-16 sonar works quite well for edge detection
2025-07-16 changed to .cpp files for debugging with oled, extended boiler plate code, fixed header guard issue
    [main.cpp, pin_out.h, state_machine.cpp]
2025-07-16 even more boiler plate
2025-07-18 first working button press state machine with a timed return
2025-07-18 pet on ground works
2025-07-19 the magnetic encoder works!
2025-07-20 sensors and actuators header files sorted out
2025-07-20 refactored actuators and sensors, all compiles
2025-07-21 implemented the magnetic encoder
2025-07-21 sonar implemented
2025-07-21 magnetic encoder implemented as pid, still needs to be tested and tuned
2025-07-21 implemented the return pets state, and fixed the direction issue with the base gear
    [BaseGear.cpp, pwm_config.h, state_return_pets.cpp]
2025-07-21 implemented claw and retreat strategy
2025-07-21 implemented tape following state and fixed a bit masking issue in the mag encoder code
    [BaseGear.cpp, MagneticEncoder.cpp, state_machine.cpp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]
2025-07-23 updates pin-out and removed the rotary encoder and start button
2025-07-24 pin out updated to reflect mounted motors
2025-07-27 schematic and footprints finished
    [motherboard.kicad_pcb, motherboard.kicad_sch]
2025-07-27 more schematics going to happen
    [motherboard.kicad_sch]
2025-07-28 actuator classes fully implemented, TODOs added
2025-07-29 actuators and sensors finished and tests compile
2025-07-31 sonar and cascade tests ran
2025-08-01 mag ok, base gear tuned
2025-08-03 tested hardware timer
2025-08-04 state machine tof lag is an issue
    [Arm.h, BaseGear.cpp, BaseGear.h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]
2025-08-04 fixed base gear pid
    [BaseGear.cpp, pwm_config.h, state_tape_following.cpp]
2025-08-05 tof algorithm needs modification, but crashing no longer an issue
    [BaseGear.cpp, main.cpp, state_machine.cpp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]
2025-08-06 arm in bucket start, tweaking needed for the tof, and consider the wall
2025-08-06 bucket lifts
2025-08-07 base gear issue resolved: pwm frequency too high
    [BaseGear.h, Motor.cpp, pwm_config.h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]
2025-08-07 changing the pwm freq messes with the tape following, scrambling the channels fixes itgit commit
    [pwm_config.h, state_machine.cpp, state_tape_following.cpp]
2025-08-07 pwm channel to timers configured correctly
    [Servo.h, pwm_config.h, state_machine.cpp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]
